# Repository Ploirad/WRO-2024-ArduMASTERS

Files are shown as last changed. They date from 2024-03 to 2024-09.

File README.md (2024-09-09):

<p align="center">
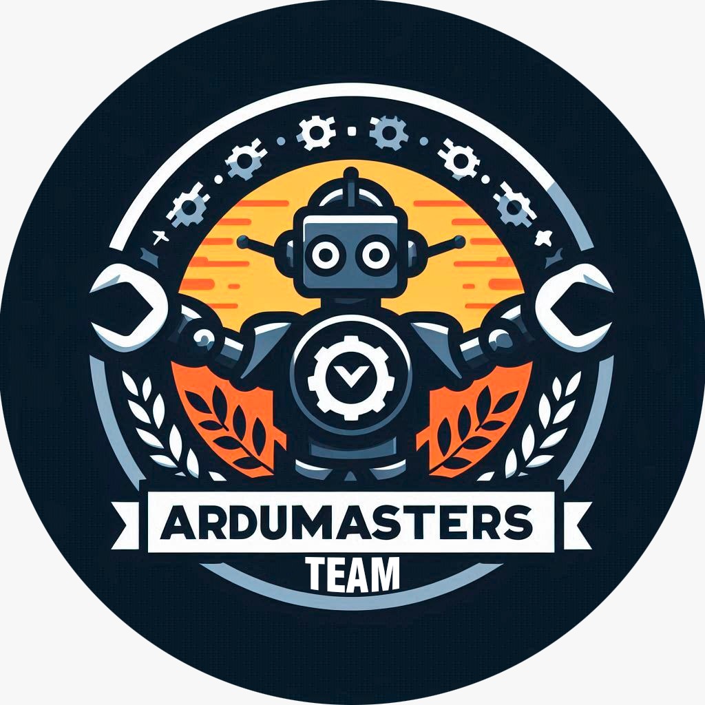
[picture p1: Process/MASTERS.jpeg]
  
</p> 

# Index
- [Members of the team](#members-and-collaborators-of-the-team)
- [Files](#files)
- [Building instructions](#building-instructions)
  1. [Components](#1-components)
  2. [Scheme](#2-make-the-scheme)
  3. [Print the 3d models](#3-print-the-3d-models)
  4. [Chassis assemble](#4-chassis-assemble)
      - [Base](#1-base)
      - [Stub axles](#2-stub-axles)
      - [Zipper](#3-zipper)
      - [Wheels and dc motors](#4-wheels-and-dc-motors)
      - [Gear and servo](#5-gear-and-servo)
      - [Battery shield and spacers](#6-battery-sield-and-spacers)
  5. [Software installation](#5-software-installation)
      - [OS installation and adjustment](#1-os-installation-and-adjustment)
      - [Auto login configuration](#2-auto-login-configuration)
      - [Update packages](#3-update-packages)
      - [Install python](#4-install-python)
      - [Install basic libraries](#5-install-basic-libraries-for-the-camera-machine-vision-and-tcs34725)
      - [Enable the i2c for the tcs34725](#6-enable-the-i2c-bus-for-the-tcs34725)
      - [Download our github repository](#7-download-our-github-repository)
      - [Automate the entrance into the repository](#8-automate-the-entrance-into-the-repository)
      - [Useful commands](#9-useful-commands)
  6. [Ending](#6-ending)

# Members and collaborators of the team
- Darío López Parada (born on June 24, 2008)
- Pablo Pietro Remartínez (born on November 25, 2007)
- Adrían Yago Benitez (born on August 3, 2009)
- Miguel Amez Riendas (born on Dicember 8, 1988)(he is our coach)
- Marío Torreiro Sevilla (born on March 14, 2008)
- Francisco Javier Abajo Alonso (born on August 21, 2008)
>The last two of us are only collaborators because are going to participate at the start but they are doing the pilgrims route to Santiago de Compostela
# Files
## [models](https://github.com/Ploirad/WRO-2024-ArduMASTERS/tree/main/models)
  In this folder we got all the 3D models that are and were on the car
## [other](https://github.com/Ploirad/WRO-2024-ArduMASTERS/tree/main/other)  
  In this folder we got our logo and a logbook based in the months
## [schemes](https://github.com/Ploirad/WRO-2024-ArduMASTERS/tree/main/schemes)
  In this folder we got the electric scheme
## [src](https://github.com/Ploirad/WRO-2024-ArduMASTERS/tree/main/src)
  In this folder we got all the source codes that we use and used on the team.
## [t-photos](https://github.com/Ploirad/WRO-2024-ArduMASTERS/tree/main/t-photos)
  In this folder we got the image of our team.
## [v-photos](https://github.com/Ploirad/WRO-2024-ArduMASTERS/tree/main/v-photos)
  In this folder we got images from all the parts of our car.
## [video](https://github.com/Ploirad/WRO-2024-ArduMASTERS/tree/main/video)
  In this folder we got two video of our car while it is moving in the different challenges

# Building instructions
## 1. Components
   
  - [Raspberry Pi 4 model b](https://www.amazon.es/Raspberry-Modelo-Cortex-A72-1-50GHz-Bluetooth/dp/B0CJ4XHZ4G/ref=sr_1_5?sr=8-5)
  - [L298N](https://www.amazon.es/HiLetgo®-Bridge-Stepper-Controller-Arduino/dp/B07CHBRF4Z/ref=sr_1_6?__mk_es_ES=ÅMÅŽÕÑ&crid=3CJEWNNVPNLVR&dib=eyJ2IjoiMSJ9.J1IoI4lcmBqTeHP6767NOPyHf44YnyBlMhRhNQmwhLPTvn-dkeFWVvZ24iSLNdLEsOo4ooBlprGz448954UpMxjdS0bdiWc1hwVDBXMP-t9t4_4KgoZEEybMySz0g1oxw-xZU3EWznA39EtTB1fHM7-nmBE-2RSX3PxZOuCamckWiUSHLKjgWUtkx_Y0LoXIWijt19YuN4BcRkwKV_2o7n2GrYa19QQ4jJWNpDryZuy2crPCVqmgHsKvyNFtU_g5ow7OvmKWSF_494XvJaVbwU5s7gRYqkgwMPjXoGPJd48.9j7OLBLKW3YQo2MtQQEm8taLG9BbZ2LkyE7f1IlGtZ0&dib_tag=se&keywords=l298n&qid=1723974557&sprefix=l298n%2Caps%2C188&sr=8-6)
  - [DC Motors](https://www.amazon.es/dp/B0B3D789V3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)
  - [Servo MG996R](https://es.aliexpress.com/item/1005006223358432.html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)
  - [18650 Battery](https://es.aliexpress.com/item/1005007228231597.html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,scm-url:1007.40000.327270.0,pvid:d4def50f-37a6-4321-8474-3b1b2da490f3,tpp_buckets:668%232846%238109%231935&pdp_npi=4%40dis%21EUR%2112.57%211.25%21%21%2196.80%219.68%21%40211b619a17239759870871818e9591%2112000039883706387%21rec%21ES%212755819411%21X&utparam-url=scene%3ApcDetailTopMoreOtherSeller%7Cquery_from%3A)
  - [18650 Shield](https://es.aliexpress.com/item/1005005986332436.html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,scm-url:1007.40000.327270.0,pvid:a7e2a1ef-289c-4358-9af2-3f99fd0d2d7a,tpp_buckets:668%232846%238110%231995&pdp_npi=4%40dis%21EUR%216.19%212.01%21%21%2147.54%2115.43%21%402103835c17163972291436621eb662%2112000035190946401%21rec%21ES%213002009838%21&utparam-url=scene%3ApcDetailTopMoreOtherSeller%7Cquery_from%3A)
  - [Dupond Cables](https://www.amazon.es/240Piezas-Breadboard-compatible-Arduino-Raspberry/dp/B0BRMKX5RT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)
  - [HC-SR04](https://www.amazon.es/sspa/click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)
  -   [Pi Camera](https://www.amazon.es/AZDelivery-c%C3%A1mara-para-Raspberry-Pi/dp/B01M6UCEM5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)

## 2. Make the [scheme](https://github.com/Ploirad/WRO-2024-ArduMASTERS/blob/main/Schemes/WRO_Car.jpg)

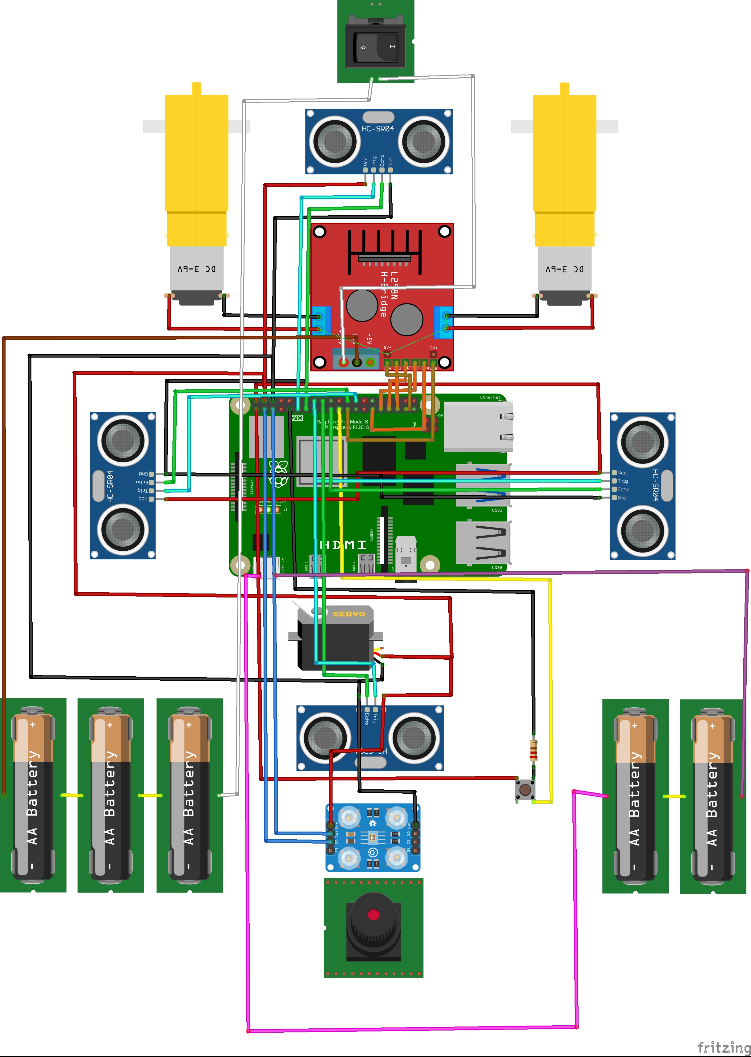
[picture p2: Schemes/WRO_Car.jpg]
Schemes


>The color sensor sown in the image it's just for reference the model thar we are really using it's the TCS34725

## 3. Print the 3D models

You will need to 3D print the models in the repository ['Models/Current_Car_Models'](https://github.com/Ploirad/WRO-2024-ArduMASTERS/tree/main/Models/Current_Car_Models). In our case we have used an Ender 3, an Artillery Sidewinder X4 Pro and a Prusa Mk3s for printing the chassis out. But you can use any printer of your preference. These parts don't need to support any abnormal forces therefore can be printed in any material. In our case we printed them with PLA.  

## 4. Chassis assemble

Once we have all the parts printed it's time to put them together. Now we will show you how to.

### 1. Base
 
 Base

 First of all we place the raspberry and L298N on the base at their places:  
- The Raspberry is placed transversaly in the middle of the car.  
- The L298N is placed at the back of the car in between the motors.

### 2. Stub axels

Stub axels

Now we place the stub axels, this will serve to transfer the rotation of the servo to the wheels to vary their direction.  
- We insert a M3 nut in each stub axel for later on
- We place the part in the hollow rods that stick out of the chassis upwards, as shown in the picture.
- We fix it in place with a M3 x 20 screw and washer, and screw it to a M3 nut at the botton of the car.

> Be careful with the hollow rod is extremly fragile.  
> Do not apply any unnecessary forces on it until it is screwed.  

### 3. Zipper

Zipper

Next is the install of the zipper this will syncronize the direction of bowth sides and transfer the servo direction.  
- We place the zipper as shown in the picture above and screw it with a M3 screw and nut in each side.

### 4. Wheels and DC motors

Now we mount the four wheels to the chassis
- The two frontal ones are drilled trough the middle and fixed in placed with a M3 screw.
- We fix the two DC motors in place using glue.
- The two in the back are simply snapped in place.  

### 5. Gear and servo

Gear

To finish the direction we place the gear and the servo which will guide all the direction system.  
- We insert the gear in the servo and screw it in place
- We place the servo in it's place with the gear on top of the zipper. And fix it in place with glue.  

### 6. Battery sield and spacers

Cage_spacers

Finally we install the battery in place to power everything up.
- We glue the four spacers in place being careful to aling the holes as much as posible.
- We screw the battery shield trouhg the spacers and the usb looking to the front of the car.  

## 5. Software installation

Now that we have all the hardware redy to go, we need a "brain" to move it.  
So here we will guide you command by command how to setup your raspberry pi in order to work correctly with the hardware.

### 1. OS installation and adjustment

1. Install [Raspberry Pi Imager](https://www.raspberrypi.com/software/) on your computer.



2. Download the [Raspberry Pi OS Lite](https://www.raspberrypi.com/software/operating-systems/).



3. Open Imager.



4. Select your model of Raspberry. In our case it's Raspberry Pi 4.



5. Select the OS image we downloaded before.




6. Select the SD card in wich we are going to intall the OS.



7. Click the "Next" buttom. And click in "Edit Settings".




8. Configure username, password and WIFI. And click on "Save".



9. Click on "Yes".




> Be carefull this proccess will erase all the information saved on the SD card.

10. Insert the SD card in to the Raspberry and power it up.



### 2. Auto-login configuration

1. Enter raspberry pi configuration.  
-       sudo raspi-config



2. Enter in system options.



3. Enter in Boot / Auto Login.



4. Enter in Console Autologin.



### 3. Update packages
-      sudo apt update & sudo apt upgrade -y



### 4. Install Python
-      sudo apt install python3-pip
  


### 5. Install basic libraries for the camera, machine vision and tcs34725
-     sudo apt install python3-picamera
      sudo apt install python3-opencv
      sudo pip3 install adafruit-circuitpython-tcs34725
      sudo pip3 install adafruit-blinka

### 6. ENABLE THE I2C BUS FOR THE TCS34725
1. Enter raspberry pi configuration.
-       sudo raspi-config
2. Select interface options

Tcs_1

3. Select P5 I2C

Tcs_2

4. Enable it

Tcs_3

### 7. Download our github repository
1. Install git.
-      sudo apt install git



2. Create directory for the repository.
-     mkdir WRO-2024-ArduMASTERS
      cd WRO-2024-ArduMASTERS
      git init
      git remote add origin https://github.com/Ploirad/WRO-2024-ArduMASTERS.git
      git config core.sparseCheckout true
      echo "Src/" >> .git/info/sparse-checkout



3. Download repository
-      git pull origin main



### 8. Automate the entrance into the repository
1. Open the rc.local file
-       sudo nano /etc/rc.local

2. Put this command before exit 0, replacing USER_NAME to the name of the user
-        su - USER_NAME -c "cd /home/USER_NAME/WRO-2024-ArduMASTERS/Src/Main; /usr/bin/python3 /home/USER_NAME/WRO-2024-ArduMASTERS/Src/Main/MAIN.py >> /tmp/Main_output 2>&1 &"
3f58c6ed-0c3e-40fc-b18e-0f1019878ab6

3. Reboot to verify changes
-      sudo reboot

### 9. Useful commands
1. Update repository
-      git pull origin main
2. Run code
-      python3 "file name"
3. See files in current directory
-      ls
4. Go to directory
-      cd "directory name"
5. Go to the previous directory
-      cd ../
6. See the output in a ssh conection
-      tail -f /tmp/Main_output
7. Kill the process
   1. See the number of the process
   -      ps aux | grep python3
   

   2. Use the command kill to destroy the process
   -      kill NUMBER_OF_THE_PROCESS
   

# 6. Ending

After reboot your car shoud work like the videos of this [readme.md](https://github.com/Ploirad/WRO-2024-ArduMASTERS/tree/main/video) in the video folder.

If you want to test the different componets or recalibrate the camera go to [test codes](https://github.com/Ploirad/WRO-2024-ArduMASTERS/tree/main/Src/Test%20codes)

I hope that this guide has been useful, if you have some problemens, do not doubt about talking with us.

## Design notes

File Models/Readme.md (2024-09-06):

<p align="center">
  
</p>

<b>
<h1>Summary:
  </h1></b>

In this folder we got all the things that are related to de chasis of the robot, including older ones that were discarded.
Here you find two inter folders:

# [Old_Car_Models](https://github.com/Ploirad/WRO-2024-ArduMASTERS/tree/main/Models/Old_Car_Models)
  This folder contains all the things that have been replaced for other ones because we think thy are not usefull or we found better ones for the car. This are:
  - [WRO Backweel.stl](https://github.com/Ploirad/WRO-2024-ArduMASTERS/blob/main/Models/Old_Car_Models/WRO%20Backweel.stl)
  - [WRO Battery Squad.stl](https://github.com/Ploirad/WRO-2024-ArduMASTERS/blob/main/Models/Old_Car_Models/WRO%20Battery%20Squad.stl)
  - [WRO Chassis.stl](https://github.com/Ploirad/WRO-2024-ArduMASTERS/blob/main/Models/Old_Car_Models/WRO%20Chassis.stl)
  - [WRO Chock Direction.stl](https://github.com/Ploirad/WRO-2024-ArduMASTERS/blob/main/Models/Old_Car_Models/WRO%20Chock%20Direction.stl)
  - [WRO Direction wheel ok.stl](https://github.com/Ploirad/WRO-2024-ArduMASTERS/blob/main/Models/Old_Car_Models/WRO%20Direction%20wheel%20ok.stl)
  - [WRO Front Wheel.stl](https://github.com/Ploirad/WRO-2024-ArduMASTERS/blob/main/Models/Old_Car_Models/WRO%20Front%20Wheel.stl)
  - [WRO L. Stub Axle.stl](https://github.com/Ploirad/WRO-2024-ArduMASTERS/blob/main/Models/Old_Car_Models/WRO%20L.%20Stub%20Axle.stl)
  - [WRO Lateral Ultrasound Supports.stl](https://github.com/Ploirad/WRO-2024-ArduMASTERS/blob/main/Models/Old_Car_Models/WRO%20Lateral%20Ultrasound%20Supports.stl)
  - [WRO Motor Support.stl](https://github.com/Ploirad/WRO-2024-ArduMASTERS/blob/main/Models/Old_Car_Models/WRO%20Motor%20Support.stl)
  - [WRO Protoboard Support.stl](https://github.com/Ploirad/WRO-2024-ArduMASTERS/blob/main/Models/Old_Car_Models/WRO%20Protoboard%20Support.stl)
  - [WRO R. Stub Axle.stl](https://github.com/Ploirad/WRO-2024-ArduMASTERS/blob/main/Models/Old_Car_Models/WRO%20R.%20Stub%20A%20xle.stl)
  - [WRO Raspberry Pi 4 Camera Box.stl](https://github.com/Ploirad/WRO-2024-ArduMASTERS/blob/main/Models/Old_Car_Models/WRO%20Raspberry%20Pi%204%20Camera%20Box.stl)
  - [WRO Raspberry Pi 4 Camera Support.stl](https://github.com/Ploirad/WRO-2024-ArduMASTERS/blob/main/Models/Old_Car_Models/WRO%20Raspberry%20Pi%204%20Camera%20Support.stl)
  - [WRO Raspberry Pi Support.stl](https://github.com/Ploirad/WRO-2024-ArduMASTERS/blob/main/Models/Old_Car_Models/WRO%20Raspberry%20Pi%20Support.stl)
  - [WRO Rear Drive Sprocket.stl](https://github.com/Ploirad/WRO-2024-ArduMASTERS/blob/main/Models/Old_Car_Models/WRO%20Rear%20Drive%20Sprocket.stl)
  - [WRO Servo Box.stl](https://github.com/Ploirad/WRO-2024-ArduMASTERS/blob/main/Models/Old_Car_Models/WRO%20Servo%20Box.stl)
  - [WRO Servo Support.stl](https://github.com/Ploirad/WRO-2024-ArduMASTERS/blob/main/Models/Old_Car_Models/WRO%20Servo%20Support.stl)
  - [WRO Servo Transmission Pinion.stl](https://github.com/Ploirad/WRO-2024-ArduMASTERS/blob/main/Models/Old_Car_Models/WRO%20Servo%20Transmission%20Pinion.stl)
  - [WRO Steering Wheel Nut.stl](https://github.com/Ploirad/WRO-2024-ArduMASTERS/blob/main/Models/Old_Car_Models/WRO%20Steering%20Wheel%20Nut.stl)
  - [WRO Stub Axle Support.stl](https://github.com/Ploirad/WRO-2024-ArduMASTERS/blob/main/Models/Old_Car_Models/WRO%20Stub%20Axle%20Support.stl)
  - [WRO Ultrasonic Sensor Box.stl](https://github.com/Ploirad/WRO-2024-ArduMASTERS/blob/main/Models/Old_Car_Models/WRO%20Ultrasonic%20Sensor%20Box.stl)
  - [WRO Wheel Cap.stl](https://github.com/Ploirad/WRO-2024-ArduMASTERS/blob/main/Models/Old_Car_Models/WRO%20Wheel%20Cap.stl)
# [Current_Car_Models](https://github.com/Ploirad/WRO-2024-ArduMASTERS/tree/main/Models/Current_Car_Models)

  This folder contains all the things that we have in our car right now, this ones are the best ones we found for our car. This are:
  - [WRO Bumper.stl](https://github.com/Ploirad/WRO-2024-ArduMASTERS/blob/main/Models/Current_Car_Models/WRO%20Bumper.stl)
  - [WRO Camera Support 2.0.stl](https://github.com/Ploirad/WRO-2024-ArduMASTERS/blob/main/Models/Current_Car_Models/WRO%20Camera%20Support%202.0.stl)
  - [WRO Car_Headlights.stl](https://github.com/Ploirad/WRO-2024-ArduMASTERS/blob/main/Models/Current_Car_Models/WRO%20Car_Headlights.stl)
  - [WRO Car_v15.stl](https://github.com/Ploirad/WRO-2024-ArduMASTERS/blob/main/Models/Current_Car_Models/WRO%20Car_v15.stl)
  - [WRO HC-SR04 support.stl](https://github.com/Ploirad/WRO-2024-ArduMASTERS/blob/main/Models/Current_Car_Models/WRO%20HC-SR04%20support.stl)
  - [WRO Pi_support.stl](https://github.com/Ploirad/WRO-2024-ArduMASTERS/blob/main/Models/Current_Car_Models/WRO%20Pi_support.stl)
  - [WRO Steering_bar.stl](https://github.com/Ploirad/WRO-2024-ArduMASTERS/blob/main/Models/Current_Car_Models/WRO%20Steering_bar.stl)

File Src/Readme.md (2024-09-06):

<p align="center">
  
</p>

# Summary:
In this foder we put all the codes that we [had done](https://github.com/Ploirad/WRO-2024-ArduMASTERS/tree/main/Src/diary) over time, the main code that its working right now is in [this folder](https://github.com/Ploirad/WRO-2024-ArduMASTERS/tree/main/Src/Main) and these are the [codes](https://github.com/Ploirad/WRO-2024-ArduMASTERS/tree/main/Src/Test%20codes) we use to calibrate and test all our sensors.

# [Diary](https://github.com/Ploirad/WRO-2024-ArduMASTERS/tree/main/Src/diary)

  This folder contains all the codes that we have been doing all the curse for our robot. Here you can find this codes, where we have grouped the similar ones by versions:
  >There we put only the lastest version, if you wanna see everything and its description see this [link](https://github.com/Ploirad/WRO-2024-ArduMASTERS/tree/main/Src/diary#files)
  - [Camera color detection v2.0.0.py](https://github.com/Ploirad/WRO-2024-ArduMASTERS/blob/main/Src/diary/camera_color_detection_v2.0.0.py)
  - [Camera color extractor.py](https://github.com/Ploirad/WRO-2024-ArduMASTERS/blob/main/Src/diary/camera_color_extractor.py)
  - [Color detector with movement.py](https://github.com/Ploirad/WRO-2024-ArduMASTERS/blob/main/Src/diary/color_detector_with_movement.py)
  - [Engine.py](https://github.com/Ploirad/WRO-2024-ArduMASTERS/blob/main/Src/diary/engine.py)
  - [Servos test v1.1.py](https://github.com/Ploirad/WRO-2024-ArduMASTERS/blob/main/Src/diary/servos_test_v1.1.0.py)
  - [Ultrasound v1.1.py](https://github.com/Ploirad/WRO-2024-ArduMASTERS/blob/main/Src/diary/ultrasound_v1.1.0.py)

  Our folder is :
  ## [Mains](https://github.com/Ploirad/WRO-2024-ArduMASTERS/tree/main/Src/Mains)
  This is a internal folder that contains all of our old mains.
  - [Main v1.0.py](https://github.com/Ploirad/WRO-2024-ArduMASTERS/blob/main/Src/diary/Mains/main_v1.0.py)
  - [Main v1.1.py](https://github.com/Ploirad/WRO-2024-ArduMASTERS/blob/main/Src/diary/Mains/main_v1.1.py)
  - [Main v1.2.py](https://github.com/Ploirad/WRO-2024-ArduMASTERS/blob/main/Src/diary/Mains/main_v1.2.py)
  - [Main v1.3.py](https://github.com/Ploirad/WRO-2024-ArduMASTERS/blob/main/Src/diary/Mains/main_v1.3.py)

# [Main](https://github.com/Ploirad/WRO-2024-ArduMASTERS/tree/main/Src/Main)
  There we have all the codes that we are using right now in our car.
  - ## [Json]()
    - [CAM.json](https://github.com/Ploirad/WRO-2024-ArduMASTERS/blob/main/Src/Main/CAM.json)
    - [Move.josn](https://github.com/Ploirad/WRO-2024-ArduMASTERS/blob/main/Src/Main/Move.json)
    - [tcs_color_detection.json](https://github.com/Ploirad/WRO-2024-ArduMASTERS/blob/main/Src/Main/tcs_color_detection.json)
  - ## [Libraries](https://github.com/Ploirad/WRO-2024-ArduMASTERS/tree/main/Src/Main/Libraries)
    - [Boton.py](https://github.com/Ploirad/WRO-2024-ArduMASTERS/blob/main/Src/Main/Libraries/Boton.py)
    - [End_rounds.py](https://github.com/Ploirad/WRO-2024-ArduMASTERS/blob/main/Src/Main/Libraries/End_rounds.py)
    - [MOTOR_DRIVER](https://github.com/Ploirad/WRO-2024-ArduMASTERS/blob/main/Src/Main/Libraries/MOTOR_DRIVER.py)
    - [Movement_Functions.py](https://github.com/Ploirad/WRO-2024-ArduMASTERS/blob/main/Src/Main/Libraries/Movement.py)
    - [New_color_detector.py](https://github.com/Ploirad/WRO-2024-ArduMASTERS/blob/main/Src/Main/Libraries/New_color_detector.py)
    - [Tcs34725.py](https://github.com/Ploirad/WRO-2024-ArduMASTERS/blob/main/Src/Main/Libraries/tcs34725.py)
  - ## [Camera_main.py](https://github.com/Ploirad/WRO-2024-ArduMASTERS/blob/main/Src/Main/Camera_Main.py)
  - ## [Movement_Main.py](https://github.com/Ploirad/WRO-2024-ArduMASTERS/blob/main/Src/Main/Movement_Main.py)
  - ## [tcs_Main.py](https://github.com/Ploirad/WRO-2024-ArduMASTERS/blob/main/Src/Main/tcs_Main.py)
  - ## [Main.py](https://github.com/Ploirad/WRO-2024-ArduMASTERS/blob/main/Src/Main/MAIN.py)
# [Proof codes](https://github.com/Ploirad/WRO-2024-ArduMASTERS/tree/main/Src/Proof%20codes)
  This folder contains all the proof codes that done for our robot.This folder is in order to test all of our components.
 - [Libraries/MOTOR_DRIVER.py](https://github.com/Ploirad/WRO-2024-ArduMASTERS/blob/main/Src/Test%20codes/Libraries/MOTOR_DRIVER.py)
 - [Camera_color_extraction.py](https://github.com/Ploirad/WRO-2024-ArduMASTERS/blob/main/Src/Test%20codes/Camera_color_extraction.py)
 - [Movement_test.py](https://github.com/Ploirad/WRO-2024-ArduMASTERS/blob/main/Src/Test%20codes/Movement_test.py)
 - [Tcs34725.py](https://github.com/Ploirad/WRO-2024-ArduMASTERS/blob/main/Src/Test%20codes/Tcs34725_test.py)
 - [Ultrasound_test.py](https://github.com/Ploirad/WRO-2024-ArduMASTERS/blob/main/Src/Test%20codes/Ultrasound_test.py)

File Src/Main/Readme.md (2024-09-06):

<p  align="center">
  
</p> 

# Files
- [Camera_Main.py](#camera_mainpy)
- [MAIN.py](#main)
- [Movement_Main.py](#movement_main)
- [Tcs_Main.py](#tcs_mainpy)

In [Libraries](https://github.com/Ploirad/WRO-2024-ArduMASTERS/tree/main/Src/Main/Libraries) we got all the functions and Json files that we use in our main files:
- [Boton.py](#botonpy)
- [End_rounds.py](#end_roundspy)
- [Movement_Functions.py](#movement_functionspy)
- [MOTOR_DRIVER.py](#motor_driverpy)
- [New_color_detector.py](#new_color_detectorpy)
- [Tcs34725.py](#tcs34725py)
- [Jsons](#jsons)
# Main
## [Camera_Main.py](https://github.com/Ploirad/WRO-2024-ArduMASTERS/blob/main/Src/Main/Camera_Main.py)
This code detect colors and calculate areas of different colors in the camera's view. This information is sent to a Json that is read by the main code. This code use the library [New_color_detector.py](https://github.com/Ploirad/WRO-2024-ArduMASTERS/blob/main/Src/Main/Libraries/New_color_detector.py).

## [MAIN.py](https://github.com/Ploirad/WRO-2024-ArduMASTERS/blob/main/Src/Main/MAIN.py)
This code is designed to control a robot's movement based on color detection and sensor data written in Json files in other mains. This code uses the libraries [MOTOR_DRIVER.py](https://github.com/Ploirad/WRO-2024-ArduMASTERS/blob/main/Src/Main/Libraries/MOTOR_DRIVER.py), [Boton.py](https://github.com/Ploirad/WRO-2024-ArduMASTERS/blob/main/Src/Main/Libraries/Boton.py), [Movement_Functions](https://github.com/Ploirad/WRO-2024-ArduMASTERS/blob/main/Src/Main/Libraries/Movement_Functions.py) and [End_rounds](https://github.com/Ploirad/WRO-2024-ArduMASTERS/blob/main/Src/Main/Libraries/End_rounds.py).

## [Movement_Main](https://github.com/Ploirad/WRO-2024-ArduMASTERS/blob/main/Src/Main/Movement_Main.py)
This code continuously measure distances using ultrasonic sensors and write the measurements to a JSON file.

## [Tcs_Main.py](https://github.com/Ploirad/WRO-2024-ArduMASTERS/blob/main/Src/Main/Tcs_Main.py)
This code is designed to detect colors using a TCS34725 color sensor and write the detection results to a JSON file. This code uses the library [tcs34725.py](https://github.com/Ploirad/WRO-2024-ArduMASTERS/blob/main/Src/Main/Libraries/tcs34725.py).

# Libraries
## [Boton.py](https://github.com/Ploirad/WRO-2024-ArduMASTERS/blob/main/Src/Main/Libraries/Boton.py)
This code detects when the starting button is pressed.

## [End_rounds.py](https://github.com/Ploirad/WRO-2024-ArduMASTERS/blob/main/Src/Main/Libraries/End_rounds.py)
This code have the functions that is used in the end of its challenge, in case of the open challenge it try to find the exact place it started, in the obstacle challenge it execute the parking function.

## [MOTOR_DRIVER.py](https://github.com/Ploirad/WRO-2024-ArduMASTERS/blob/main/Src/Main/Libraries/MOTOR_DRIVER.py)
This code makes the DC Motors move in the direction we want.

## [Movement_functions.py](https://github.com/Ploirad/WRO-2024-ArduMASTERS/blob/main/Src/Main/Libraries/Movement_Functions.py)
This code have built-in functions that controls the movement: pivot_aproximation looks if there are a traffic sign after traspassing another one, backward goes back until it can move correctly and change_direction do a 180 degrees turn if the last traffic sign is red in the end of the second lap.

## [New_color_detector.py](https://github.com/Ploirad/WRO-2024-ArduMASTERS/blob/main/Src/Main/Libraries/New_color_detector.py)
This code checks if the camera sees the colours of the traffic signs in a certain range that we gave previously.

## [Tcs34725.py](https://github.com/Ploirad/WRO-2024-ArduMASTERS/blob/main/Src/Main/Libraries/tcs34725.py)
This code reads the tcs color values and with a range of colours it returns a variable with the stimated colour.

## [Jsons](https://github.com/Ploirad/WRO-2024-ArduMASTERS/tree/main/Src/Main/Libraries/Json)
The [CAM.json](https://github.com/Ploirad/WRO-2024-ArduMASTERS/tree/main/Src/Main/Libraries/Json/CAM.json), [Move.json](https://github.com/Ploirad/WRO-2024-ArduMASTERS/tree/main/Src/Main/Libraries/Json/Move.json) and [tcs_color_detection.json](https://github.com/Ploirad/WRO-2024-ArduMASTERS/tree/main/Src/Main/Libraries/Json/tcs_color_detection.json) files stores the information of the mains.

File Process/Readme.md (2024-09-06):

<p align="center">
  
</p>

<b>
<h1>Summary:
  </h1></b>
  
In this folder we got our [logo](https://github.com/Ploirad/WRO-2024-ArduMASTERS/blob/main/Process/MASTERS.jpeg) and a [log book](https://github.com/Ploirad/WRO-2024-ArduMASTERS/tree/main/Process/logbook) of our progress and achivements during the different months.

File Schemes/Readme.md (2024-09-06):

<p align="center">
  
</p>
There we have the <a href = "https://github.com/Ploirad/WRO-2024-ArduMASTERS/blob/main/Schemes/WRO_Car.jpg">connection scheme</a> that we used in our car.
</p>
<p align="center">
 
</p>

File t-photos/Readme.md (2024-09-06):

<p align="center">
  
</p>

<b>
<h1>Summary:
  </h1><b/>

  In this folder we got the image of our [team](https://github.com/Ploirad/WRO-2024-ArduMASTERS/blob/main/t-photos/Team_photo.jpeg)

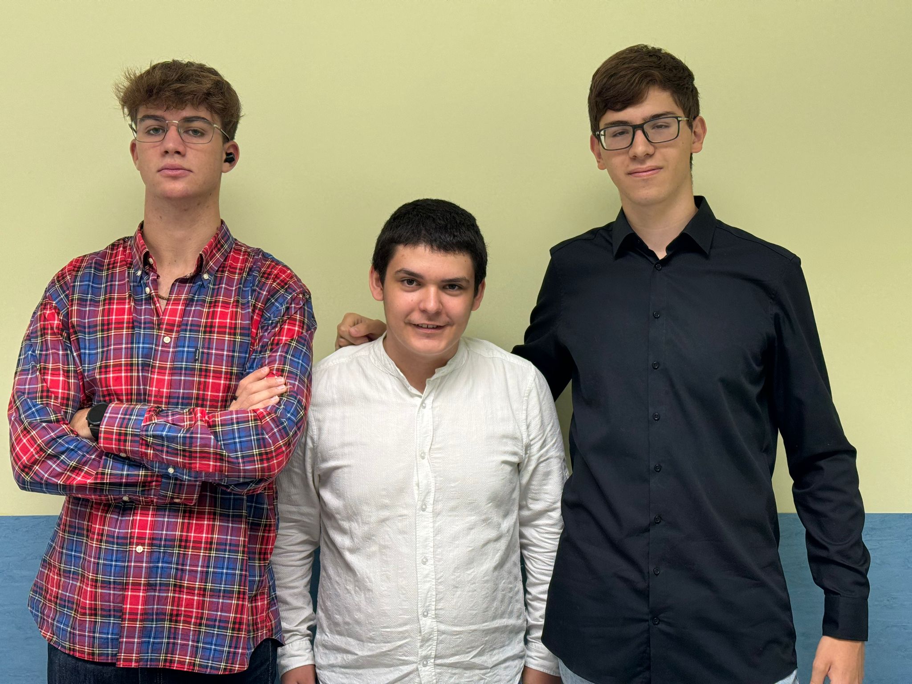
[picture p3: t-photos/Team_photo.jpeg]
Team photo


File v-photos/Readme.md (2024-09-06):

<p align="center">
  
</p>

<b>
<h1>Summary:
  </h1><b/>

  In this folder we got images of all the angles of our car:
  - [Front](https://github.com/Ploirad/WRO-2024-ArduMASTERS/blob/main/v-photos/Front_car.jpeg)
  - [Back](https://github.com/Ploirad/WRO-2024-ArduMASTERS/blob/main/v-photos/Back_car.jpeg)
  - [Up](https://github.com/Ploirad/WRO-2024-ArduMASTERS/blob/main/v-photos/Upper_car.jpeg)
  - [Under](https://github.com/Ploirad/WRO-2024-ArduMASTERS/blob/main/v-photos/Under_car.jpeg)
  - [Right](https://github.com/Ploirad/WRO-2024-ArduMASTERS/blob/main/v-photos/Right_side_car.jpeg)
  - [Left](https://github.com/Ploirad/WRO-2024-ArduMASTERS/blob/main/v-photos/Left_side_car.jpeg)
  ## Front
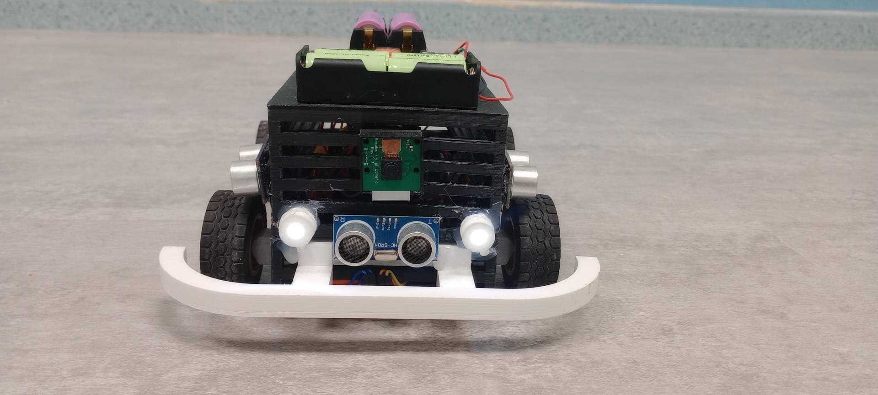
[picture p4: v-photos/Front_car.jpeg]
Front
  
  ## Back
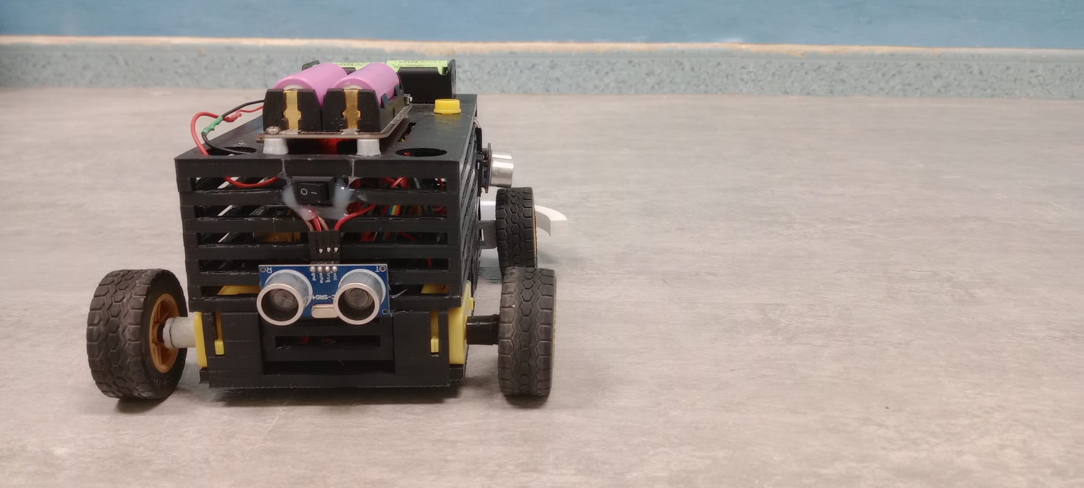
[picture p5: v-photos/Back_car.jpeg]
  
  ## Up
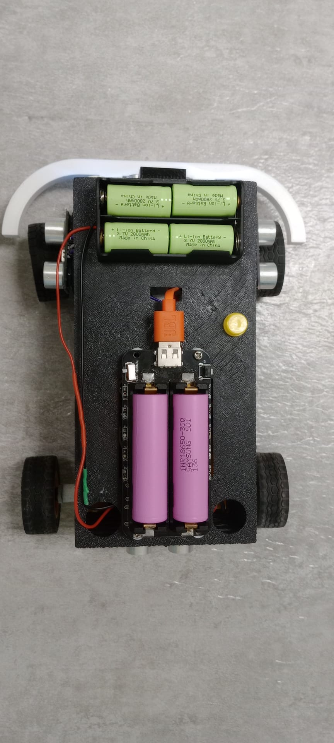
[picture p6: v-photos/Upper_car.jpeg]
  
  ## Under
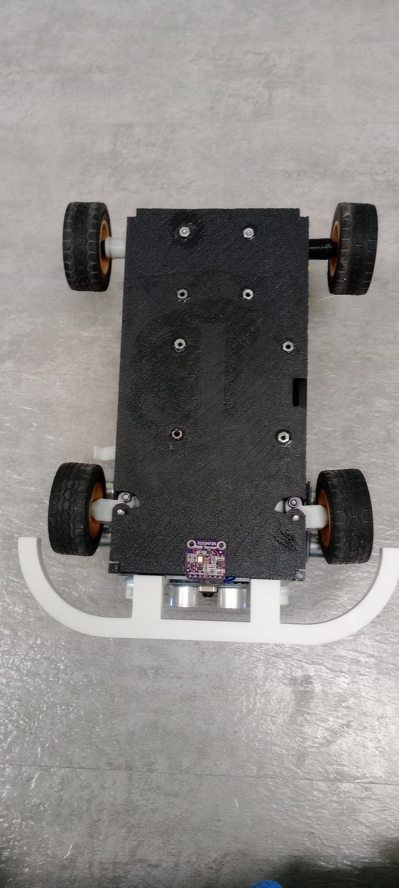
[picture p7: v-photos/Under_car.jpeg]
  
  ## Right
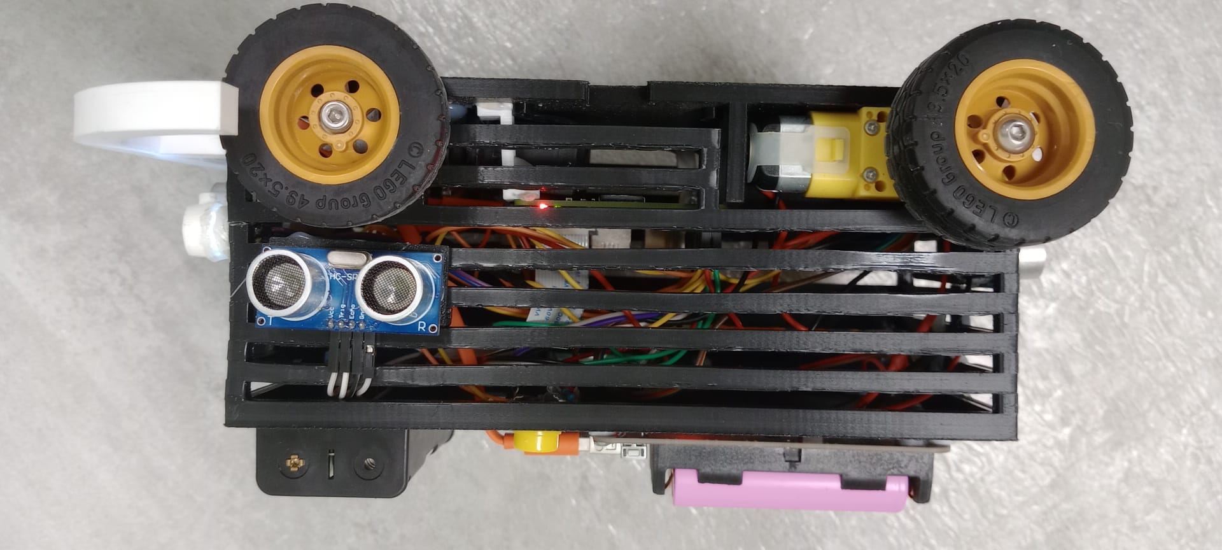
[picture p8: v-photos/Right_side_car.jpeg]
  
  ## Left
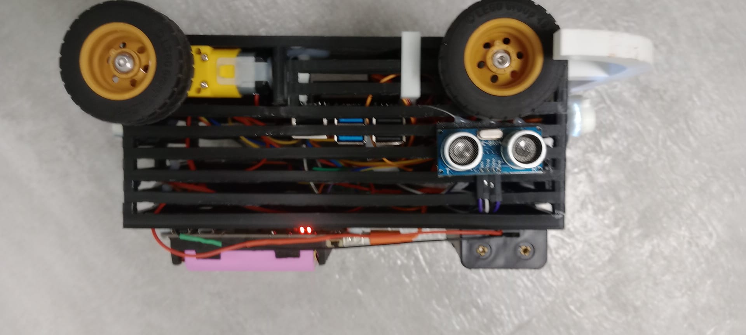
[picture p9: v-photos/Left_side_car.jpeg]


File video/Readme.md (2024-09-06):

<p align="center">
  
</p>

<b>
<h1>Summary:
  </h1><b/>

  In this folder we got a video of our [car moving by itself](https://www.youtube.com/watch?v=2Q0AEukgsb0) in the first lap of the first challenge.
> Click in the link of "car moving by itself" if you want to see the video.

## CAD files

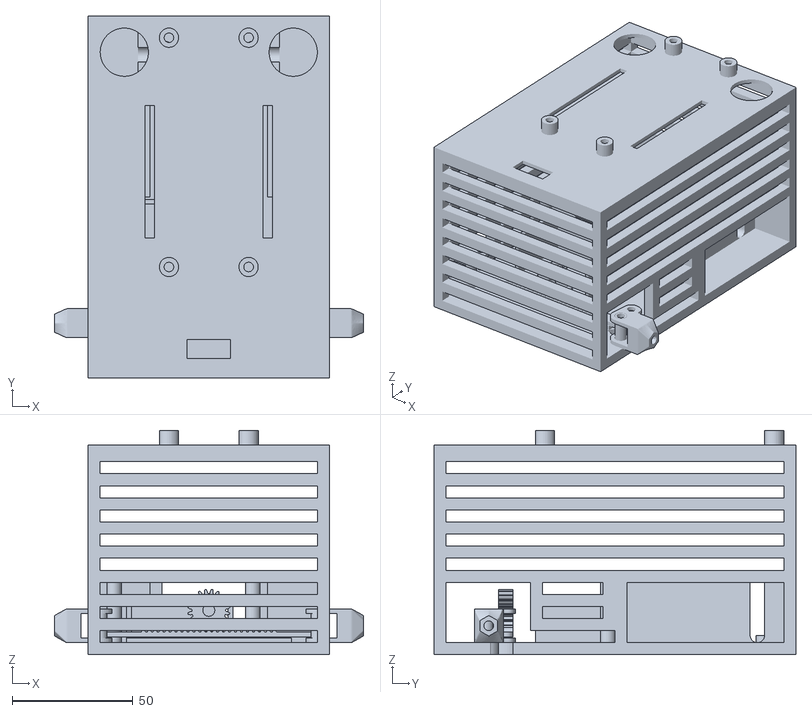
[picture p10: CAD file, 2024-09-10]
Models/Current_Car_Models/Coche WRO v21.stl
128.2 x 150.0 x 93.0

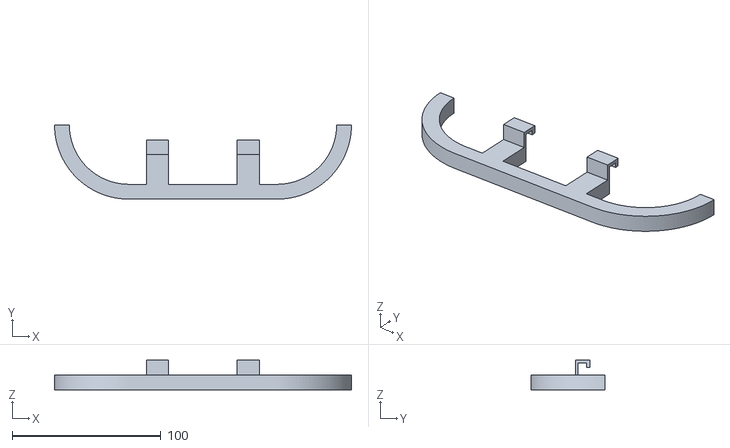
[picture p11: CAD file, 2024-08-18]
Models/Current_Car_Models/WRO Bumper.stl
200.0 x 50.0 x 20.0

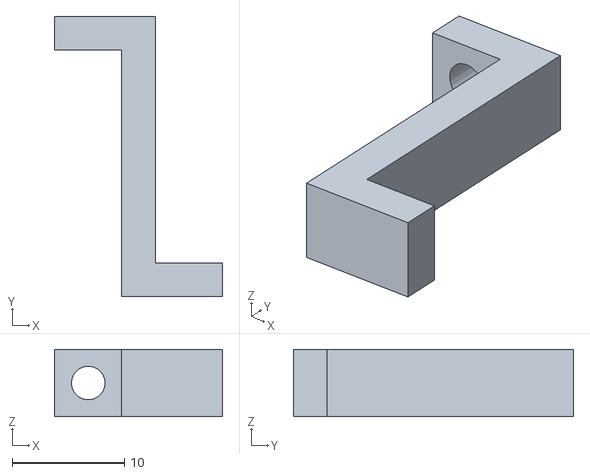
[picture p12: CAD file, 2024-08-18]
Models/Current_Car_Models/WRO Pi_support.stl
15.0 x 25.0 x 6.00

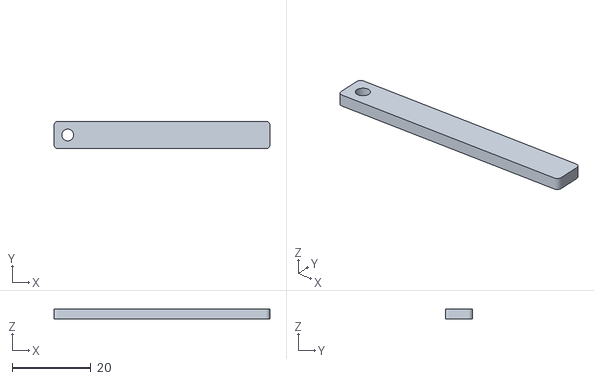
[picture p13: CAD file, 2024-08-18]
Models/Current_Car_Models/WRO Steering_bar.stl
55.0 x 7.00 x 2.50

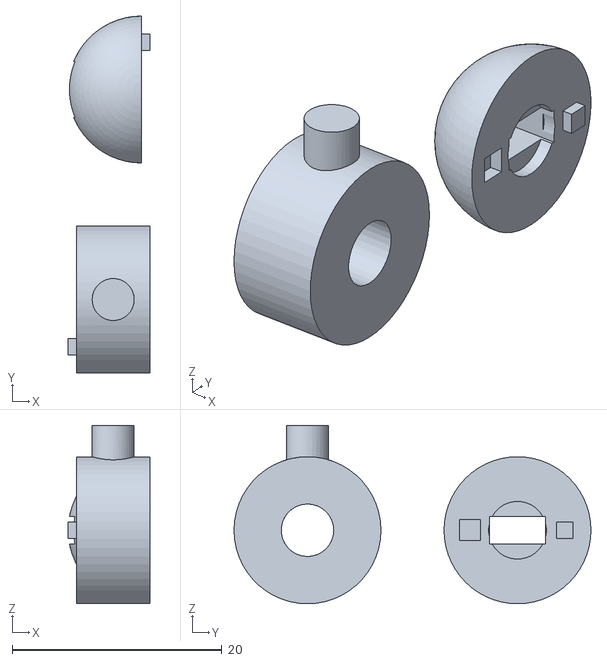
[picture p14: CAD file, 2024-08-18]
Models/Current_Car_Models/WRO Car_Headlights.stl
7.80 x 34.0 x 17.0

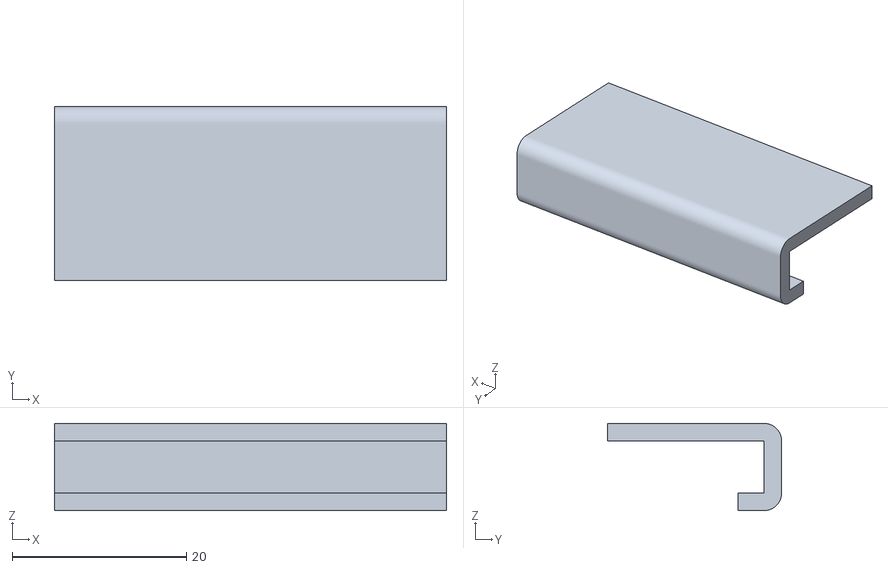
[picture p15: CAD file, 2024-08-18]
Models/Current_Car_Models/WRO HC-SR04 support.stl
45.0 x 20.0 x 10.0

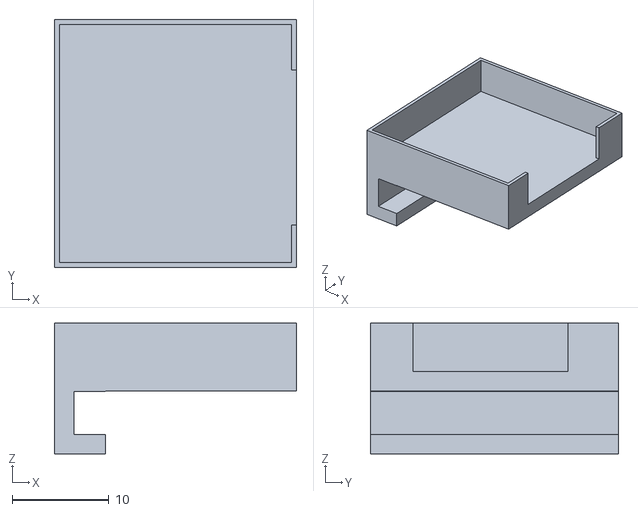
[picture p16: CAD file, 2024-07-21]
Models/Current_Car_Models/WRO Camera Support 2.0.stl
25.0 x 25.6 x 13.5

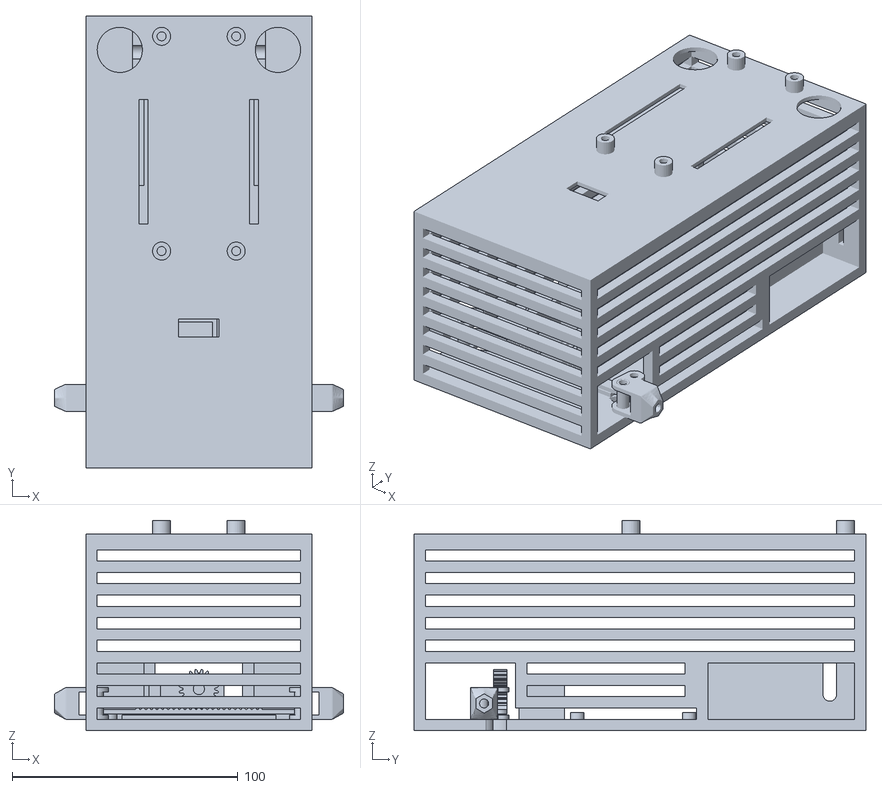
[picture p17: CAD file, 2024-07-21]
Models/Current_Car_Models/WRO Car_v15.stl
128.1 x 200.0 x 93.0

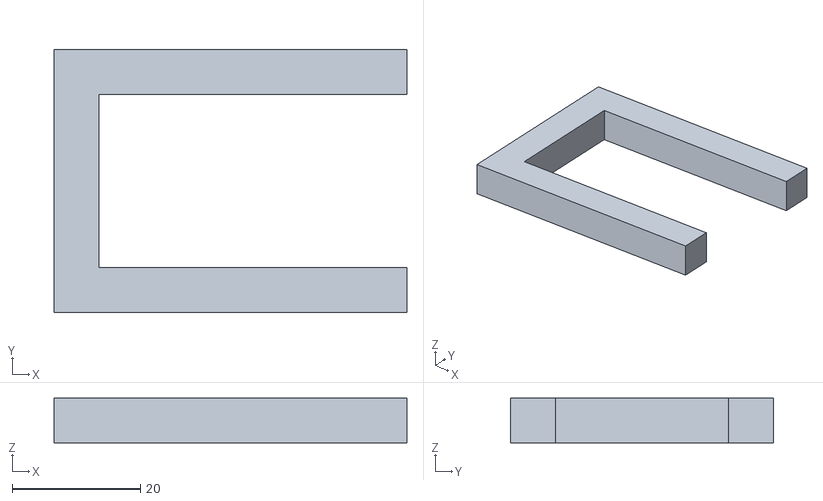
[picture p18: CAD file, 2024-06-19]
models/Current_Car_Models/WRO Servo Support.stl
55.0 x 41.0 x 7.00

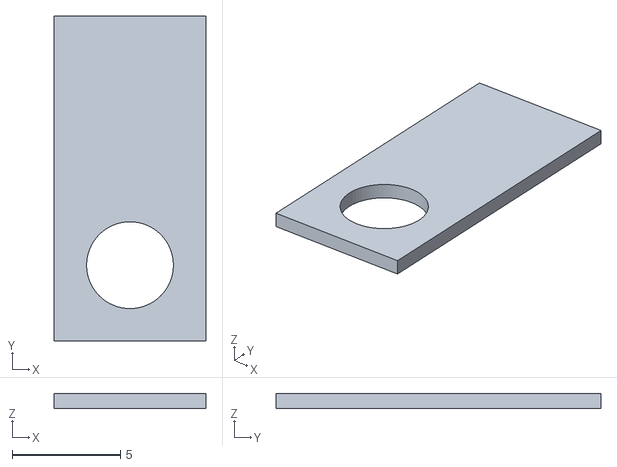
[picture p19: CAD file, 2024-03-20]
models/Current_Car_Models/WRO Chock Direction.stl
7.00 x 15.0 x 0.7

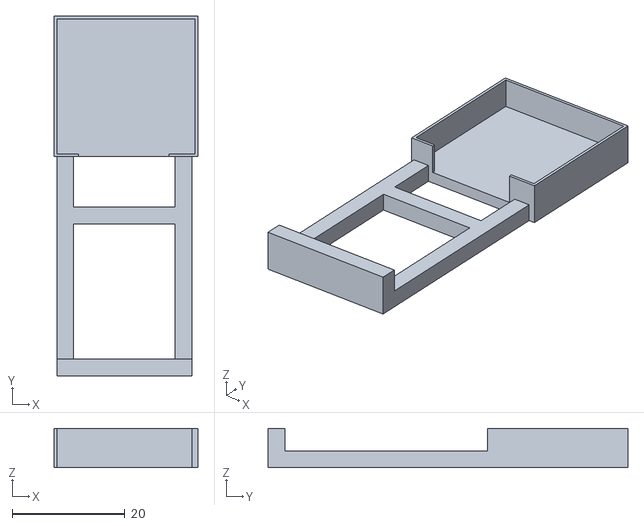
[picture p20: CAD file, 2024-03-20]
models/Current_Car_Models/WRO Raspberry Pi 4 Camera Support.stl
25.6 x 64.0 x 7.00

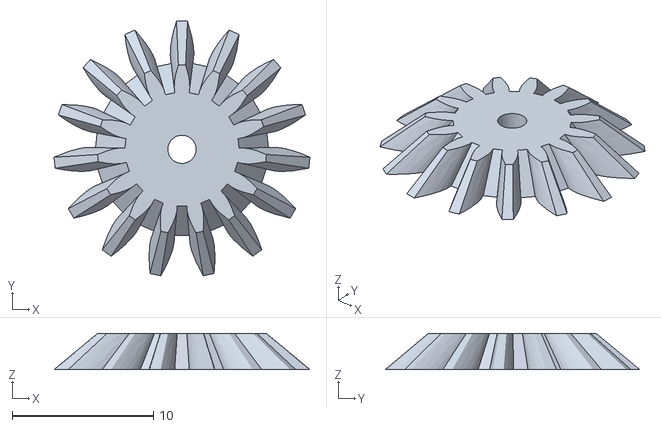
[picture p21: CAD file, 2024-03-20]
models/Current_Car_Models/servo transmission pinion.stl
18.1 x 18.0 x 2.55

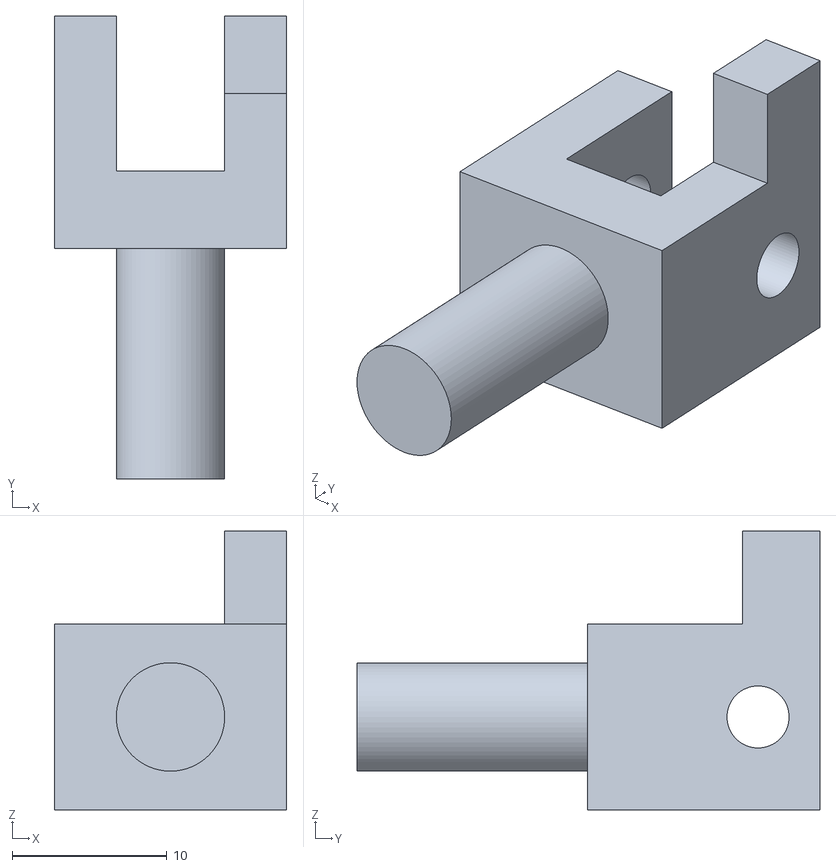
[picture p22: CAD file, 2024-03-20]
models/Current_Car_Models/WRO R. Stub A xle.stl
15.0 x 29.9 x 18.0

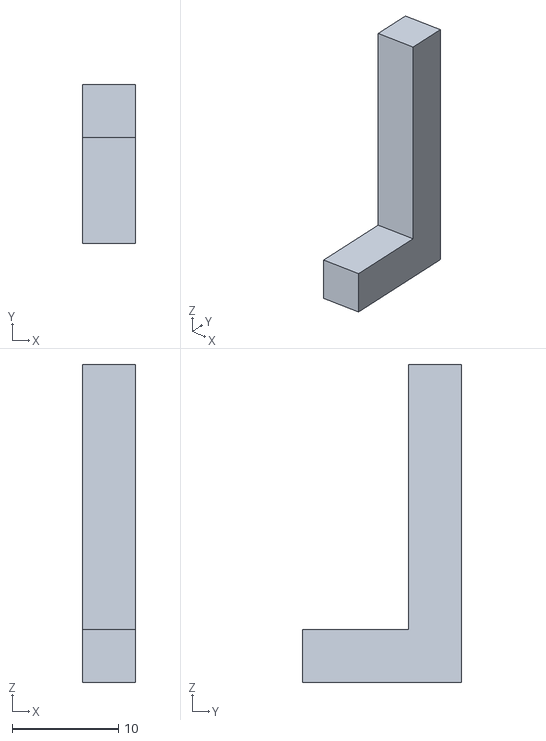
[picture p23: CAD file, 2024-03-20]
models/Current_Car_Models/WRO Battery Squad.stl
5.00 x 15.0 x 30.0

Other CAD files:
models/Current_Car_Models/WRO Motor Support.stl
models/Current_Car_Models/WRO L. Stub Axle.stl
models/Current_Car_Models/WRO Raspberry Pi 4 Camera Box.stl
models/Current_Car_Models/WRO Raspberry Pi Support.stl
Models/Old_Car_Models/WRO Backweel.stl
Models/Old_Car_Models/WRO Chassis.stl
Models/Old_Car_Models/WRO Direction wheel ok.stl
Models/Old_Car_Models/WRO Front Wheel.stl
Models/Old_Car_Models/WRO L. Stub Axle.stl
Models/Old_Car_Models/WRO Lateral Ultrasound Supports.stl
Models/Old_Car_Models/WRO Motor Support.stl
Models/Old_Car_Models/WRO Protoboard Support.stl
Models/Old_Car_Models/WRO Raspberry Pi 4 Camera Box.stl
Models/Old_Car_Models/WRO Raspberry Pi Support.stl
Models/Old_Car_Models/WRO Rear Drive Sprocket.stl
Models/Old_Car_Models/WRO Servo Box.stl
Models/Old_Car_Models/WRO Steering Wheel Nut.stl
Models/Old_Car_Models/WRO Stub Axle Support.stl
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

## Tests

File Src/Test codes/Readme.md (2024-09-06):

<p align="center">
  
</p> 

# Sumary
These codes are used in order to test the different components of the ArduMASTERS 

# Files
- [Camera_color_detection_test.py](#camera_color_detection_testpy)
- [Camera_color_extractor_test.py](#camera-color-extractor-testpy)
- [Movement_test.py](#movement_testpy)
- [Tc34725_test.py](#tcs34725_testpy))
- [Ultrasound.py](#ultrasound_testpy)

> I don't write the file MOTOR_DRIVER in libraries becouse isn't a test code

# Test codes
## [Camera_color_detection_test.py](https://github.com/Ploirad/WRO-2024-ArduMASTERS/blob/main/Src/Test%20codes/camera_color_detection_test.py)
This code is used to show a cloud of points of the green, red and magenta in different windows is used in conjuction with the next code.

## [Camera color extractor test.py](https://github.com/Ploirad/WRO-2024-ArduMASTERS/blob/main/Src/Test%20codes/Camera_color_extractor_test.py)
This code is used for extract a color from a photo, then it print the highest and lowest value in [HSV](https://pro.arcgis.com/es/pro-app/latest/help/analysis/raster-functions/color-model-conversion-function.htm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,admite%20entradas%20de%203%20bandas) and put in the camera a cloud of points with its centroid in the range of color.

If you want to adjust the colors go to [this file](https://github.com/Ploirad/WRO-2024-ArduMASTERS/blob/main/Src/Main/Libraries/New_color_detector.py) and put your values in the spaces marked in green in the photo.

Foto camara

> Where we have "alto" means the highest value and "bajo" the lowest one.

> WARNING the first codes can only run in a rasberry pi with enviroment or x.

## [Movement_test.py](https://github.com/Ploirad/WRO-2024-ArduMASTERS/blob/main/Src/Test%20codes/Movement_test.py)

This code ask you in the terminal the percentage of direction and traction and move the car according to the inputs.

## [Tcs34725_test.py](https://github.com/Ploirad/WRO-2024-ArduMASTERS/blob/main/Src/Test%20codes/Tcs34725_test.py)

This code prints the values of the tcs34725 and its color based in aproximated values, being unknown if the code isn't one that we want.

## [Ultrasound_test.py](https://github.com/Ploirad/WRO-2024-ArduMASTERS/blob/mainV2/Src/Test%20codes/Ultrasound_test.py)

This code prints the distance value of the four HC sensors.

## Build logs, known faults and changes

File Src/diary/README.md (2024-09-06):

<p  align="center">
  
</p> 

# Files:
These ones are the [old funtions](#old-functions)
  - [Camera_color_detection_v1.0.0](#camera_color_detection_v100py)
  - [Camera_color_detection_v1.1.0](#camera_color_detection_v110py)
  - [Camera_color_detection_v1.1.1](#camera_color_detection_v111py)
  - [Camera_color_detection_v2.0.0](#camera_color_detection_v200py)
  - [Camera_color_extractor](#camera_color_extractorpy)
  - [Color_detector_with_movement](#color_detector_with_movementpy)
  - [Engine](#enginepy)
  - [Servos_test_v1.0.0](#servos_test_v100py)
  - [Servos_test_v1.1.0](#servos_test_v110py)
  - [Ultrasound_v1.0.0](#ultrasound_v100py)
  - [Ultrasound_v1.1.0](#ultrasound_v110py)
  - [Set_servo_in_0]()

These ones are the [old mains](#old-mains)
  - [Main_v1.0](#main_v10py)
  - [Main_v1.1](#main_v11py)
  - [Main_v1.2](#main_v12py)
  - [Main_v1.3](#main_v13py)

# Old functions

## [Camera_color_detection_v1.0.0.py](https://github.com/Ploirad/WRO-2024-ArduMASTERS/tree/main/Src/diary/camera_color_detection_v1.0.0.py)
This code is a library used to find the range of a color in an image and return another image with the color painted white as its center.

## [Camera_color_detection_v1.1.0.py](https://github.com/Ploirad/WRO-2024-ArduMASTERS/tree/main/Src/diary/camera_color_detection_v1.1.0.py)
This code does the same thing as its [previous version](https://github.com/Ploirad/WRO-2024-ArduMASTERS/tree/main/Src/diary/camera_color_detection_v1.0.0.py), but use a different way in order to calculate the center and its less modulated.

## [Camera_color_detection_v1.1.1.py](https://github.com/Ploirad/WRO-2024-ArduMASTERS/tree/main/Src/diary/camera_color_detection_v1.1.1.py)
This code, unlike its [last version](https://github.com/Ploirad/WRO-2024-ArduMASTERS/tree/main/Src/diary/camera_color_detection_v1.1.0.py), does everything in its own code and shows how it sees the different colors in real time.

## [Camera_color_detection_v2.0.0.py](https://github.com/Ploirad/WRO-2024-ArduMASTERS/tree/main/Src/diary/camera_color_detection_v2.0.0.py)
This code is simpler than the [previous version](https://github.com/Ploirad/WRO-2024-ArduMASTERS/tree/main/Src/diary/camera_color_detection_v1.1.1.py) and works with the computer's camera instead of the Raspberry Pi's.

## [camera_color_extractor.py](https://github.com/Ploirad/WRO-2024-ArduMASTERS/tree/main/Src/diary/camera_color_extractor.py)
This code let us select a section of a camera, and it highlights evry part of the camera between these range.
>We had made it with HSV instead of RGB becouse with HSV we can detect the saturation and the tone.

## [Color_detector_with_movement.py](https://github.com/Ploirad/WRO-2024-ArduMASTERS/tree/main/Src/diary/color_detector_with_movement.py)
That code is our first of combining the use of the motors and the camera.
>Its so raw that we don't consider it as a main code.

## [Engine.py](https://github.com/Ploirad/WRO-2024-ArduMASTERS/tree/main/Src/diary/engine.py)
This code is a library that was used to control the motors of our car.

## [Servos_test_v1.0.0.py](https://github.com/Ploirad/WRO-2024-ArduMASTERS/tree/main/Src/diary/servos_test_v1.0.0.py)
This code is in order to test the servos movement 

## [Servos_test_v1.1.0.py](https://github.com/Ploirad/WRO-2024-ArduMASTERS/tree/main/Src/diary/servos_test_v1.1.0.py)
This code is the same than its [previous version](https://github.com/Ploirad/WRO-2024-ArduMASTERS/tree/main/Src/diary/servos_test_v1.0.0.py), but we add a button.

## [Set_servo_in_0.py](https://github.com/Ploirad/WRO-2024-ArduMASTERS/tree/main/Src/diary/set_servo_in_0.py)
This code is in order to set the servo in 0 degree.

## [Ultrasound_v1.0.0.py](https://github.com/Ploirad/WRO-2024-ArduMASTERS/tree/main/Src/diary/ultrasound_v1.0.0.py)
That code is an ultrasound test.

## [Ultrasound_v1.1.0.py](https://github.com/Ploirad/WRO-2024-ArduMASTERS/tree/main/Src/diary/ultrasound_v1.1.0.py)
This code its the same than its [previous version](https://github.com/Ploirad/WRO-2024-ArduMASTERS/tree/main/Src/diary/ultrasound_v1.0.0.py) but everything its in a functions, making it as a library.

# Old mains 
## [Main_v1.0.py](https://github.com/Ploirad/WRO-2024-ArduMASTERS/blob/main/Src/diary/Mains/main_v1.0.py)
This code is our first main code. This code detects colored objects and decides the movement based on the object position, using ultrasonic sensors too.

## [Main_v1.1.py](https://github.com/Ploirad/WRO-2024-ArduMASTERS/blob/main/Src/diary/Mains/main_v1.1.py)
This code its the same than its [previous version](https://github.com/Ploirad/WRO-2024-ArduMASTERS/blob/main/Src/diary/Mains/main_v1.0.py) but it have a more detailed color detection system and it doesn't use the ultrasonic sensors.

## [Main_v1.2.py](https://github.com/Ploirad/WRO-2024-ArduMASTERS/blob/main/Src/diary/Mains/main_v1.2.py)
This code add to its [last version](https://github.com/Ploirad/WRO-2024-ArduMASTERS/blob/main/Src/diary/Mains/main_v1.1.py) a button activation, a parking feature and use again the ultrasonic sensors.

## [Main_v1.3.py](https://github.com/Ploirad/WRO-2024-ArduMASTERS/blob/main/Src/diary/Mains/main_v1.3.py)
This code is a rework of its [previous version](https://github.com/Ploirad/WRO-2024-ArduMASTERS/blob/main/Src/diary/Mains/main_v1.2.py) and we changed the prints and the comments, in order to making it easier to understand and its more modular.

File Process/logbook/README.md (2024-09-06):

<p align="center">
  
</p>
This is a diary where we write down all our progress and achievements across the months:

# Months:
- [October](#October)
- [November](#November)
- [Dicember](#Dicember)
- [January](#January)
- [February](#February)
- [March](#March)
- [April](#April)
- [May](#May)
- [June](#June)
- [July](#July)

  > Most of the times the commits were only made during Wednesday because it's the only time we have robotics class

## October
During October, we had read the rules in order to view what we should do (we didn't start until January becouse until that month the rules weren't updated), we also learnt how to use git and created this repository.

## November
In November we were still learning how to manage git by making a script with random library in three different branches and then merging them.

## Dicember
During Dicember, we had learnt how to use the PiCamera and we also finished the programm.

## January
In January we made the connections and we alredy had the competition rules, so we divide the work and we had created scripts for the engine and for the camara, but the last one didn't work well.
## February
During February, we had learnt how to manage a readme, we created the first car model, we improve the engine script too, we create our logo.
## March
In March, we did some test such as GPIO, ultrasounds, servos, camera with the library PiCamera 2, that we later removed due to malfunction; we did the first attempt of the main code too, we also had updated the stl files of our car models and improved a little bit the Readme's.
## April
During April, we essentially learnt how to work with Open CV due to the malfunction of the camera I had mentioned before.
## May
In May, we created a camera version that finally works well, we done our first version of the parking, we improved the first version of the main code too and we clean the code making the main code able to access a new folder where we keep all the functions used in the main.

At this time one mate joined to us but another one left us.
## June
During June, we solved some bugs, created a new car model, we also added a tcs34725 (a color detector) and changed again the main codes according with the cleaner code system.
## July
In July, we reworked the main code, making it work in threads, a more optimized way, we also changed some readme, and refactored the files.

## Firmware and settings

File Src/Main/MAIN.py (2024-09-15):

import json
import time
from Libraries import MOTOR_DRIVER as MD
from Libraries import Boton as B
import Libraries.Movement_Functions as F
import Libraries.End_rounds as End
import math as M

button_pressed = False
time_to_90_degrees = 5
half_turn = False

if __name__ == "__main__":
    while True:
        try:
            if button_pressed:
               with open(os.path.join(os.path.dirname(__file__), "Libraries", "Json", "CAM.json"),  "r", encoding="utf-8") as C:
                    cam_data = json.load(C)

                    color = cam_data["Color"]
                    ignore = cam_data["Ignore"]
                    
                    RC = cam_data["RedC"]
                    GC = cam_data["GreenC"]
                    MC = cam_data["MagentaC"]
                
                    RA = cam_data["MArea"]
                    GC = cam_data["GArea"]
                    MA = cam_data["MArea"]

                    parking = cam_data["Parking"]

                with open(os.path.join(os.path.dirname(__file__), "Libraries", "Json", "tcs_color_detection.json"), "r", encoding="utf-8") as T:
                    tcs_data = json.load(T)

                    orientation = tcs_data["first_color_obteined"]
                    floor_color = tcs_data["color_obteined"]
                    turns = tcs_data["turns"]
                    laps = tcs_data["laps"]

                with open(os.path.join(os.path.dirname(__file__), "Libraries", "Json", "Move.json"), "r", encoding="utf-8") as M:
                    HC_data = json.load(M)

                    HC0 = HC_data["HC0"]
                    HC1 = HC_data["HC1"]
                    HC2 = HC_data["HC2"]
                    HC3 = HC_data["HC3"]

                if laps == 1 and  turns == 3 and orientation == floor_color:
                    if last_sign == "red":
                        F.change_direction()
                        half_turn = True
                
                if laps >= 3:
                        if parking == True:
                            End.parking(half_turn)
                        else:
                            End.home_sweet_home()

                if ignore == True:

                    if floor_color == "unknown" or floor_color == "gray":
                        
                        if HC1 <= (HC1 + HC3)/2 - 10:
                            MD.move(25,-100)
                        if HC3 <= (HC1 + HC3)/2 - 10:
                            MD.move(25,100)
                        else:
                            MD.move(25,0)
                    
                    else:
                        if floor_color == "blue":
                            MD.move(25, -100)
                            time.sleep(time_to_90_degrees)
                    
                        elif floor_color == "orange":
                            MD.move(25, 100)
                            time.sleep(time_to_90_degrees)

                else:
                    if color == "green" or color== "red":
                        last_sign = F.pivot_aproximation(color)
            else:
                if B.button_state() == True:
                    print("Button pressed")
                    button_pressed = True
        except Exception as e:
            print(e)

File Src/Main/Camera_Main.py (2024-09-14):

from Libraries import New_color_detector as CAM
from picamera import PiCamera
from picamera.array import PiRGBArray
import time
import threading
import signal
import sys
import json
import os

green_centroid = None
red_centroid = None
magenta_centroid = None
green_area = 0
red_area = 0
magenta_area = 0
camera = CAM.camera
camera.framerate = 30 #65
camera.resolution = (640, 480)
raw_capture = PiRGBArray(camera, size=(640, 480))

def principal_logic(areas):
    max_area = max(areas, key=areas.get)
    calculo = (areas[max_area] - areas['magenta'])

    traction = 25
    direction = 0
    ignore = True
    if max_area == "green" and areas[max_area] > 0:
        direction = -100
        ignore = False
    elif max_area == "red" and calculo > 0:
        direction = 100
        ignore = False
    elif max_area == "magenta" and areas[max_area] > 1000:
        ignore = False

    return traction, direction, max_area, ignore, calculo

def detect(stop_event):
    park = False
    while not stop_event.is_set():
        try:
            for frame in camera.capture_continuous(raw_capture, format="bgr", use_video_port=True):
                image = frame.array
                height, width = image.shape[:2]
                lower_half = image[height//2:, :]
                _, green_area = CAM.detect_green(lower_half)
                _, red_area = CAM.detect_red(lower_half)
                magenta_centroid, magenta_area = CAM.detect_magenta(lower_half)
            
                color_areas = {"green": green_area, "red": red_area, "magenta": magenta_area}

                t, d, color, ignore, calculo = principal_logic(color_areas)
                
                if color == "magenta":
                    park = True
                else:
                    park = False

                color = "" if ignore else color

                data = {
                        "Color": color,
                        "Parking": park,
                        "TRACTION": t,
                        "DIRECTION": d,
                        "MagentaC": magenta_centroid,
                        "GArea": green_area,
                        "RArea": red_area,
                        "MArea": magenta_area,
                        "Calculo": calculo
                    }
                raw_capture.truncate(0)
                with open(os.path.join(os.path.dirname(__file__), "Libraries", "Json", "CAM.json"), "w", encoding='utf-8') as j:
                    json.dump(data, j, indent=4, ensure_ascii=False)
        except  Exception as e:
                print(f"Error: {e}")


def signal_handler(sig, frame):
    global stop_event
    stop_event.set()

# Create and start the threads
threads = []
stop_event = threading.Event()
signal.signal(signal.SIGINT, signal_handler)

try:
    t = threading.Thread(target=detect, args=(stop_event,))
    t.start()
    threads.append(t)

    # Wait for the end of the threads (in this case it doesn't happen unless interrupted)
    for t in threads:
        t.join()

except Exception as e:
    print(f"Error: {e}")

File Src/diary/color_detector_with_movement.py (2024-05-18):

import RPi.GPIO as GPIO
import time
from picamera import PiCamera
from picamera.array import PiRGBArray
import cv2
import numpy as np

# Definición de pines GPIO
TRIG_PIN_DELANTE = 23
ECHO_PIN_DELANTE = 24
TRIG_PIN_ATRAS = 17
ECHO_PIN_ATRAS = 27
TRIG_PIN_IZQUIERDA = 22
ECHO_PIN_IZQUIERDA = 10
TRIG_PIN_DERECHA = 5
ECHO_PIN_DERECHA = 6
servo_pin_direccion = 2
servo_pin_traccion = 3
button_pin = 9

# Configuración de GPIO
GPIO.setmode(GPIO.BCM)
GPIO.setup(TRIG_PIN_DELANTE, GPIO.OUT)
GPIO.setup(ECHO_PIN_DELANTE, GPIO.IN)
GPIO.setup(TRIG_PIN_ATRAS, GPIO.OUT)
GPIO.setup(ECHO_PIN_ATRAS, GPIO.IN)
GPIO.setup(TRIG_PIN_IZQUIERDA, GPIO.OUT)
GPIO.setup(ECHO_PIN_IZQUIERDA, GPIO.IN)
GPIO.setup(TRIG_PIN_DERECHA, GPIO.OUT)
GPIO.setup(ECHO_PIN_DERECHA, GPIO.IN)
GPIO.setup(servo_pin_direccion, GPIO.OUT)
GPIO.setup(servo_pin_traccion, GPIO.OUT)
GPIO.setup(button_pin, GPIO.IN, pull_up_down=GPIO.PUD_DOWN)

# Inicialización de la cámara
camera = PiCamera()
camera.resolution = (640, 480)
rawCapture = PiRGBArray(camera, size=(640, 480))
time.sleep(0.1)
def detect_colors(frame):
    hsv_frame = cv2.cvtColor(frame, cv2.COLOR_BGR2HSV)

    # Nuevos rangos de color
    lower_red = np.array([174, 175, 120])
    upper_red = np.array([176, 212, 170])
    lower_green = np.array([57, 104, 100])
    upper_green = np.array([65, 156, 150])
    lower_magenta = np.array([164, 148, 120])
    upper_magenta = np.array([167, 185, 170])

    # Detección de colores
    mask_red = cv2.inRange(hsv_frame, lower_red, upper_red)
    mask_green = cv2.inRange(hsv_frame, lower_green, upper_green)
    mask_magenta = cv2.inRange(hsv_frame, lower_magenta, upper_magenta)

    # Aplicar operaciones morfológicas para mejorar la detección
    kernel = np.ones((5, 5), np.uint8)
    mask_red = cv2.morphologyEx(mask_red, cv2.MORPH_OPEN, kernel)
    mask_green = cv2.morphologyEx(mask_green, cv2.MORPH_OPEN, kernel)
    mask_magenta = cv2.morphologyEx(mask_magenta, cv2.MORPH_OPEN, kernel)

    # Encontrar contornos y calcular centroides y dimensiones
    centroids_red = None
    dimensions_red = None
    cx_r = None
    Ar = None
    contours_red, _ = cv2.findContours(mask_red, cv2.RETR_EXTERNAL, cv2.CHAIN_APPROX_SIMPLE)
    if contours_red:
        contour = max(contours_red, key=cv2.contourArea)
        M = cv2.moments(contour)
        if M["m00"] != 0:
            cx = int(M["m10"] / M["m00"])
            cy = int(M["m01"] / M["m00"])
            centroids_red = [(cx, cy)]
            x, y, w, h = cv2.boundingRect(contour)
            dimensions_red = [(w, h)]
            Ar = w*h
            cx_r = cx

    centroids_green = None
    dimensions_green = None
    cx_v = None
    Av = None
    contours_green, _ = cv2.findContours(mask_green, cv2.RETR_EXTERNAL, cv2.CHAIN_APPROX_SIMPLE)
    if contours_green:
        contour = max(contours_green, key=cv2.contourArea)
        M = cv2.moments(contour)
        if M["m00"] != 0:
            cx = int(M["m10"] / M["m00"])
            cy = int(M["m01"] / M["m00"])
            centroids_green = [(cx, cy)]
            x, y, w, h = cv2.boundingRect(contour)
            dimensions_green = [(w, h)]
            Av = w*h
            cx_v = cx

    centroids_magenta = None
    dimensions_magenta = None
    cx_m = None
    Am = None
    contours_magenta, _ = cv2.findContours(mask_magenta, cv2.RETR_EXTERNAL, cv2.CHAIN_APPROX_SIMPLE)
    if contours_magenta:
        contour = max(contours_magenta, key=cv2.contourArea)
        M = cv2.moments(contour)
        if M["m00"] != 0:
            cx = int(M["m10"] / M["m00"])
            cy = int(M["m01"] / M["m00"])
            centroids_magenta = [(cx, cy)]
            x, y, w, h = cv2.boundingRect(contour)
            dimensions_magenta = [(w, h)]
            Am = w*h
            cx_m = cx

    return [mask_red, mask_green, mask_magenta], [cx_r, cx_v, cx_m], [dimensions_red, dimensions_green, dimensions_magenta], [Ar, Av, Am]


# Bucle principal
for frame in camera.capture_continuous(rawCapture, format="bgr", use_video_port=True):
    # Captura de imagen
    image = frame.array

    # Detección de colores y análisis de imagen
    masks, cx, dimensions, A = detect_colors(image)

    # Mostrar las máscaras de color y la imagen original en ventanas separadas con tamaños personalizados
    cv2.namedWindow("Original", cv2.WINDOW_NORMAL)
    cv2.resizeWindow("Original", 400, 300)
    cv2.imshow("Original", image)
    
    cv2.namedWindow("Red Mask", cv2.WINDOW_NORMAL)
    cv2.resizeWindow("Red Mask", 400, 300)
    cv2.imshow("Red Mask", masks[0])
    
    cv2.namedWindow("Green Mask", cv2.WINDOW_NORMAL)
    cv2.resizeWindow("Green Mask", 400, 300)
    cv2.imshow("Green Mask", masks[1])
    
    cv2.namedWindow("Magenta Mask", cv2.WINDOW_NORMAL)
    cv2.resizeWindow("Magenta Mask", 400, 300)
    cv2.imshow("Magenta Mask", masks[2])

    Am, Ar, Av = A[2], A[0], A[1]  # Cambiar el orden
    if Am is None:
        Am = 0
    if Ar is None:
        Ar = 0
    if Av is None:
        Av = 0

    cx_v, cx_r, cx_m = cx[1], cx[0], cx[2]
    if cx_v is None:
        cx_v = 320
    if cx_r is None:
        cx_r = 320
    if cx_m is None:
        cx_m = 320
    
    print(f"C: R:{cx[0]}, V:{cx[1]}, M:{cx[2]}")
    print(f"D: R:{Ar}, V:{Av}, M:{Am}")
    # Limpiar el búfer de captura para la siguiente imagen
    rawCapture.truncate(0)
    if cx_v < 170:
        print("V a la IZQ")
    elif cx_v > 170 and cx_v < 470:
        print("V al CENT")
    else:
        print("V a la DER")
    if cx_r < 170:
        print("R a la IZQ")
    elif cx_r > 170 and cx_v < 470:
        print("R al CENT")
    else:
        print("R a la DER")
    if cx_m < 170:
        print("M a la IZQ")
    elif cx_m > 170 and cx_v < 470:
        print("M al CENT")
    else:
        print("M a la DER")
    # Esperar una tecla para salir (salida si se presiona 'q')
    key = cv2.waitKey(1) & 0xFF
    if key == ord("q"):
        break

# Limpiar y cerrar las ventanas
cv2.destroyAllWindows()

# Limpiar configuraciones de GPIO
GPIO.cleanup()

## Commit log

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2024-02-04 Add files via upload
    Commit of the arduino file that controls two 180 servos, two 360 servos and two ultrasonic sensors.
2024-02-21 Add files via upload
    We put every 3D design
    [WRO Backweel.stl, WRO Chassis.stl, WRO Chock Direction.stl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]
2024-02-28 Moved WRO Wheel Cap.stl to models
    [WRO Wheel Cap.stl]
2024-02-28 Moved WRO Backweel.stl to models
    [WRO Backweel.stl]
2024-03-06 Rename WRO Chassis.stl to WRO Chassis.stl
    [WRO Chassis.stl]
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2024-03-06 Moved WRO L. Stub Axle.stl to models
    [WRO L. Stub Axle.stl]
2024-03-06 Rename WRO Chock Direction to WRO Chock Direction.stl
    [WRO Chock Direction.stl]
2024-03-06 Rename WRO Front Wheel to WRO Front Wheel.stl
    [WRO Front Wheel.stl]
2024-03-06 Moved WRO R.Stub Axle.stl to models
    [WRO R. Stub A xle.stl]
2024-03-06 Moved WRO Rear Drive Sprocket.stl to models
    [WRO Rear Drive Sprocket.stl]
2024-03-06 Moved WRO Servo box.stl to models
    [WRO Servo box.stl]
2024-03-06 Moved WRO Stub Axle Support.stl to models
    [WRO Stub Axle Support.stl]
2024-03-06 Moved WRO Ultrasonic Sensor Box.stl to models
    [WRO Ultrasonic Sensor Box.stl]
2024-03-13 Rename WRO Rueda dirección ok.stl to WRO Direction wheel ok.stl
    [WRO Direction wheel ok.stl]
2024-03-13 Rename WRO TUERCA RUEDA DIRECCION.stl to WRO steering wheel nut.stl
    [WRO steering wheel nut.stl]
2024-03-13 Rename piñon transmision servo.stl to servo transmission pinion.stl
    [servo transmission pinion.stl]
2024-03-13 6 Files added to Current_Car_Models
    [WRO Battery Squad.stl, WRO Lateral Ultrasound Supports.stl, WRO Motor Support.stl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]
2024-03-13 Rename models/WRO Backweel.stl to models/Current_Car_Models/WRO Backweel.stl
    [WRO Backweel.stl]
2024-03-13 Rename models/WRO Chock Direction.stl to models/Current_Car_Models /WRO Chock Direction.stl
    [WRO Chock Direction.stl]
2024-03-13 Rename WRO Chock Direction.stl to WRO Chock Direction.stl
    [WRO Chock Direction.stl]
2024-03-13 Rename models/WRO Direction wheel ok.stl to models/Current_Car_Models/WRO Direction wheel ok.stl
    [WRO Direction wheel ok.stl]
2024-03-13 Rename models/WRO L. Stub Axle.stl to models/Current_Car_Models/WRO L. Stub Axle.stl
    [WRO L. Stub Axle.stl]
2024-03-13 Rename models/WRO R. Stub A xle.stl to models/Current_Car_Models/WRO R. Stub A xle.stl
    [WRO R. Stub A xle.stl]
2024-03-13 Rename models/WRO Rear Drive Sprocket.stl to models/Current_Car_Models/WRO Rear Drive Sprocket.stl
    [WRO Rear Drive Sprocket.stl]
2024-03-13 Rename models/WRO Servo box.stl to models/Current_Car_Models/WRO Servo box.stl
    [WRO Servo box.stl]
2024-03-13 Rename models/WRO Stub Axle Support.stl to models/Current_Car_Models/WRO Stub Axle Support.stl
    [WRO Stub Axle Support.stl]
2024-03-13 Rename models/WRO Ultrasonic Sensor Box.stl to models/Current_Car_Models/WRO Ultrasonic Sensor Box.stl
    [WRO Ultrasonic Sensor Box.stl]
2024-03-13 Rename models/WRO Wheel Cap.stl to models/Current_Car_Models/WRO Wheel Cap.stl
    [WRO Wheel Cap.stl]
2024-03-13 Rename models/WRO steering wheel nut.stl to models/Current_Car_Models/WRO steering wheel nut.stl
    [WRO steering wheel nut.stl]
2024-03-13 Rename models/WRO Chassis.stl to models/Old_Car_Models/WRO Chassis.stl
    [WRO Chassis.stl]
2024-03-13 Rename models/WRO Front Wheel.stl to models/Old_Car_Models/WRO Front Wheel.stl
    [WRO Front Wheel.stl]
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2024-04-10 Create WRO RGB Sensor.stl
    [WRO RGB Sensor.stl]
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2024-05-29 Added WRO_Servo_Support
    [WRO_Servo_Support.stl]
2024-05-29 Rename WRO_Servo_Support.stl to WRO Servo Support.stl
    [WRO Servo Support.stl]
2024-06-01 Comments in english and Main just for the 1º round
    motor librarie fixed, made som progess on the 2º main and some minor changes
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2024-06-14 come back in Motor because the progressive movement doesn't go well
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2024-06-19 Delete src/Main/Libraries/Camera.py
    It's repeated but with another name and without anything imported
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2024-07-11 create External_Libraries to take the Libraries of Boton, Extra_Functions, MOTOR_DRIVER, New_color_detector, Ultrasonidos, parking, tsc34725 and MAIN. create Read_UltraSonic_sensors to read the value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
2024-07-18 Unfactorizate all Libraries because it doesn't go well
    [MAIN.py]
2024-07-21 git push
    [Coche WRO v15.step, Coche WRO v15.stl, WRO Backweel.stl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]
2024-07-21 Renamed Soporte Camara in models/Current_Car_Models
    [WRO Camera Support 2.0.stl]
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2024-07-22 changed readme's and file names
    [Coche WRO v15.stl, WRO Backweel.stl, WRO Battery Squad.stl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]
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2024-07-24 deleted ultrasonic_deviation and fixed bugs in Main
    [MAIN.py]
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2024-07-25 fixed minor bugs in tcs_Main
    [tcs_Main.py]
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2024-07-25 updated tcs_Mainin order to check bugs
    [tcs_Main.py]
2024-07-25 changed the code in order to review some bugs
    [tcs_Main.py]
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2024-08-18 The 3d file for the distance sensor
    [WRO HC-SR04 support.stl]
2024-08-22 Rename Faros coche.stl to Car_Headlights.stl
    [Car_Headlights.stl]
2024-08-22 Rename Coche WRO v15.stl to WRO_Car_v15.stl
    [WRO_Car_v15.stl]
2024-08-22 Rename WRO Parachoques.stl to WRO_Bumper.stl
    [WRO_Bumper.stl]
2024-08-22 Rename barra direccion.stl to steering_bar.stl
    [steering_bar.stl]
2024-08-22 Rename soporte pi.stl to pi_support.stl
    [pi_support.stl]
2024-08-23 improved Src/diary/README.md, updated the logbook and models/README.md
    [WRO Bumper.stl, WRO Car_Headlights.stl, WRO Car_v15.stl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]
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2024-09-02 updated in order to check some bugs
    [MAIN.py]
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2024-09-04 bug fixed in test codes
    [camera_color_detection_v1.1.1.py]
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2024-09-05 update MAIN to use the Movement_Functions correctly
    [MAIN.py]
2024-09-06 Minor bugs fixed in Camera_Main.py
    [Camera_Main.py]
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2024-09-09 added exceptions errors for the json openings
    [Camera_Main.py, Movement_Main.py, tcs_Main.py]
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2024-09-09 Fixed the bugs of tcs_Main and Movement_main
    [Movement_Main.py, tcs_Main.py]
2024-09-09 Made easier to understand bugs in Main
    [MAIN.py]
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2024-09-10 Rename WRO Car_v15.stl to WRO Car_v15.stl
    [WRO Car_v15.stl]
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2024-09-10 "Fixed indentation and added line number to error print statement in End_rounds.py"
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2024-09-10 "Removed unnecessary variable declarations and added a print statement for front and right distances."
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
